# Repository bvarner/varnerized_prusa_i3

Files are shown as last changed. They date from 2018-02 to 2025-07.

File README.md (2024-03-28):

# Varnerized Prusa i3 3D Printer Clone

This is a project to produce a 3d printer based upon the (very excellent) work of Mr. Josef Prusa, and the 3d printing community at large.

After playing with an i3 MK2.5 my office at the time acquired I found some guides online for building your own printer inspired by the Prusa design.
Specifically, [Tom's Dolly Build](https://toms3d.org/2017/02/23/building-cheapest-possible-prusa-i3-mk2/) was highly inspiring.

I'm willing to sacrifice _some_ asthetics, a bit of performance, the 'ease' of pre-integration, and get an education for the sake of cost cutting.
As in the early heady days of the PC industry... building a 'clone' from imported components is cheaper than purchasing the fully assembled and configured machine.

## Goal of the project.

To clone a Prusa i3 with very similar mechanics, using import parts and cheaper, more-modular electronics.
My initial budget for the build is $225. With that budget, I produced a wooden framed i3 clone, using an Arduino & RAMPS board with A4988 stepper drivers, knockoff E3D V6 hotend, and an aluminum heated bed.

I have since upgraded some things considerably, in a price-conscious manner, and well behind the bleeding edge, so that I can source parts inexpensively.

This isn't just an attempt to build a clone and leave it alone. In keeping with the RepRap / Prusa mentality, my desire is to build a device that allows for replicating / designing / implementing more advanced subsequent generations.

## This Repository / Branch Strategy

The 'master' branch here will reflect the current (stable, functioning) state of the project - the machine I'm currently running, or the last state of the machine.
The 'development' branch will track be the next iteration of updates / upgrades.

# 1.3 - Volcano Hotend & Belt Tensioning
Over the years I've had problems with bearings coming loose from the x-axis ends. I held them in place with zip-ties for more than a year.
My pancake stepper with the skelestruder gave me phenomical prints, but I had many problems with stability of the hotend holding temp during high extrusion rates or aggressive part cooling fan use.

In order to print things faster (I'm sick of waiting four hours for a tiny part) and with thicker layers, I have upgraded to a Volcano knock-off hotend -- which the skelestruder supports beautifully.
I've also decided to print my entire hotend assembly in polycarbonate, as I was having multiple parts sag over time and when printing high-temp filaments (like PC or nylon).

I ended up having to upgrade to a slightly larger pancake motor, as I exceeded the torque of the tiny pancake before I exceeded the reasonable flow rate of a 0.6mm CHT volcano nozzle.

A 200g spool of PC is more than enough to print the entire extruder and omega several times over.

Credits to the folks who made these fantastic parts that I'm using:
[X-Axis](https://www.printables.com/model/394668-mk225s-x-axis-revision-with-belt-tensioner)
[Y-Axis Tensioner](https://www.printables.com/model/306303-y-axis-belt-tensioner-v2)

# 1.2 - Skelestruder.
Having some shore 95A flex filament to print, the MK3 extruder design is rubbish. I've had issues with part cooling, part visibility during print, z-axis adjustment, it's been a problem. Futhermore I get a lot of obvious print quality issues with linear advance and the direct drive extruder with 1/16th step division.
The [Skelestruder](https://www.thingiverse.com/thing:2845416) is designed to address all of that, and after having it for a few weeks, it was obvious it's a superior design.

Additionally, a friend of mine supplied me with a Prusa Mini+ filament sensor kit, which I've integrated into my build using 
this [skelestruder sensor cover](https://www.thingiverse.com/thing:4235461).

Initially I printed everything in PETG, without a silicone sock and insulation at the top of the heat block. This caused EcageS to melt a couple times, and deformed some other parts when I attempted to print Nylon at high-temperatures.
To combat this problem, I've reprinted some parts in Polycarbonate. I purchased a 200g trial spool for a reasonable fee.

* Printed Parts
    * Polycarbonate
        * SP_EcageS_r1.stl
        * SP_Omega_r2.stl
        * SP_Pinion16_r1.stl
        * SP_Pinion14_r1.stl
        * [SP_Xclamp_mk2.stl](https://www.thingiverse.com/thing:3699231)
    * PETG
        * SP_Carriage_r1.stl
        * SP_tail_b2.stl
        * SP_EcageB_r1.stl
        * SP_EcageF17_r1.stl
        * SP_Shroud_r1.stl
        * SP_Key_r1.stl
        * Inlet_ptfe_r1b.stl
        * SP_Spider17_r1.stl
        * SP_Wheel_r1.stl
        * SP_Tread56_r1.stl
        * SP_Prack_r1.stl
        * SP_Idler_r1.stl
        * SP_tensioner_b1.stl
        * SP_knob_b2.stl
        * SP_spacer_v1a4.stl
        * IR_Sensorcover_top.stl
        * IR_Sensorcover_outlet.stl
        * IR_Sensorcover_bottom.stl
        * IR_Sensor_Arm.stl
* Purchased Parts
    * [GT2 140-2GT-6](https://www.amazon.com/gp/product/B014QJBVOY/ref=ppx_yo_dt_b_asin_title_o00_s00?ie=UTF8&psc=1)
    * [Polyimide (Kapton) tape](https://www.amazon.com/gp/product/B00W3FAFP0/ref=ppx_yo_dt_b_asin_title_o04_s00?ie=UTF8&psc=1)
    * [105zz bearings](https://www.amazon.com/gp/product/B00ZHSTKCE/ref=ppx_yo_dt_b_asin_title_o07_s00?ie=UTF8&psc=1)
    * [5mmx100mm shafts](https://www.amazon.com/gp/product/B01B27MJC6/ref=ppx_yo_dt_b_asin_title_o07_s01?ie=UTF8&psc=1) I cut and shaped these with an angle grinder.
    * [12v 5015 fans](https://www.amazon.com/gp/product/B07LF1V1P1/ref=ppx_yo_dt_b_asin_title_o07_s01?ie=UTF8&psc=1) My original cooling fan died.
    * [Prusa IR filament sensor](https://www.aliexpress.com/item/32976810546.html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)
    * [Heatblock Top Insulation](https://www.amazon.com/gp/product/B075CST527/ref=ppx_yo_dt_b_asin_title_o08_s00?ie=UTF8&psc=1) I used this between the heatbreak and the heatblock.
    * [Heatblock Silicone Sock](https://www.amazon.com/gp/product/B07Q3KHL6R/ref=ppx_yo_dt_b_asin_title_o09_s00?ie=UTF8&psc=1) How did I go so many years without a silicone sock?

# 1.1.1 - Lack Table Enclosure.
Following the [prusaprinters blog post](https://blog.prusaprinters.org/cheap-simple-3d-printer-enclosure/) on building an inexpensive (hah!) enclosure for your printer I recently picked up a couple of Ikea LACK tables.
After getting local quotes for producing the 440x440 and 440x220 acrylic panels, I opted to buy a set from a vendor on Amazon who could beat the locally sourced prices.

* Printed Parts
    * PSU Shroud
        * Compatible with the Prusa Lack table mounting clip (mounting foot geometry is closer to the Prusa part)
        * Added Lack Table PSU retainer. Similar Style as the Prusa version.
        * Text rotates to the upside down orientation on the PSU Shroud if you're rendering the LACK table parts.
    * [Ikea LACK Enclosure Main Parts](https://www.thingiverse.com/thing:2864118)
    * [Frame brace replacing the PSU for the MK3](https://www.thingiverse.com/thing:2859884)
    * [60 degree heatbed cable cover for the MK3](https://www.thingiverse.com/thing:2890592)
    * [608 bearing wheels for the adjustable spool holder](https://www.thingiverse.com/thing:3791583)
    * [Prusa Enclosure Bottom Corner with more cable space](https://www.thingiverse.com/thing:3067172)
    * [IKEA Lack Table Stack Coupler](http://www.thingiverse.com/thing:3488697)
* Purchased Parts
    * #12 AWG Silicone wire. So much better to work with than THHN.
    * XT60H Connectors
    * misc. dupont connectors & hookup wire (from the scrap bin)
    * (3) IRLB3034 N-Channel Mosfets & 10k Ohm 0805 SMT Resistors.
    * 12v RGB LED 5050 Strip (I had leftovers from another home project)
* @Home Fabricated PCB For Controlling RGB LEDs
    * Check the LEDControl directory for full KiCAD project.
    * Perfect for home-based acid etching and SMT hand soldering.
    * I use the 'laser-printer hot-iron transfer' method, and it works quite well.

# 1.1.0 - More MK3 less, MK2.
Total upgrade cost was ~$75 in January 2018.

* Heat-Bed
    * I replaced my aluminum MK3 heat bed with a magnetic MK52, 12V heat bed.
    * It's not as 'flat' as the prusa originals.
    * Cost was ~$36, as opposed to the original one which was ~$8.
    * Spring steel sheet + PEI cost around another $25. At this time, I'd opt for the powder-coated textured spring steel instead.
* Extruder
    * Uses the BondTech style extruder pulleys
    * Improved part cooling
    * 5v Noctua Fan reduces ambient noise considerably
    * I did not add a filament sensor (yet) or a dust-buffer (yet).
* Electronics
    * After having beefed up the ampacity of the RAMPS 1.4a board, and replacing the heatbed mosfet, I decided to try a RAMPS 1.6 board.
    * Much better experience than the RAMPS 1.4a.
    * After 11 months of use, no over-heating issues. No fried mosfets, no fire risk. Much better electronics from that stand point.
    * Heat bed does heat slowly, a consequence of the mosfet choice on this board, from what I understand.
    * I've updated my firmware to Marlin 1.1.9, and "Varnerized" it to match the Prusa Home Screen Asthetic on the LCD.
    * Updated RAMBo cover a bit. I ended up reprinting in PETG and got much better results than with the original PLA. It also hasn't sagged and melted in my hot-box.
* Mechanics
    * Y-Axis bearing holders have been redone, and are now my own design that allows for slight play.
    * I think I've fixed the issues with the y-axis belt holder not contacting the limit switch properly.
    * Updates to the TR8_couplings have resulted in much better Z-axis stability.
    * heatbed cable cover -- based on using ring terminals and heavy gauge speaker wire -- is _very_ large compared to the MK3.

# 1.0.0 - Hybrid MK2s & MK3
The original starting point. 1 Spool of ABS, a few scraps of cabinet grade plywood, access to a working MK2, and about $165 in imported parts.

* Heat-Bed - I chose a 3mm thick aluminum MK3 (Ultimaker clone) 200x200mm.
    * This gives me a slightly smaller build area than an Original Prusa.
    * No 'fully-automatic' skew compensation.
        * The aluminum bed of the MK3 will still work for automatic z-layer leveling.
        * Guided x-y skew measurement and compensation will be required.
    * I did pony up for a sheet of PEI plastic to cover the aluminum bed and improve adhesion. That was worth it.
* Steppers - I used an inexpensive 5-pack of 5mm output shaft steppers that put out ~40n-cm of torque.
    * My Z-Axis motors require couplings to the lead screws.
    * I did pony up for T8 ACME lead screws and nuts for the Z-axis. The small cost should be worth the improved ridgidity and accuracy.
* Electronics - Arduino Mega 2650 + RAMPS 1.4a
    * Won't be nearly as nicely packaged as a mini-rambo... until I print my own case design to make it not ugly.
    * Will have to custom-compile firmware from the Marlin project.
    * More flexibility in the long-run with regards to expansion and addition of other sensors.
    * I used a 30Amp, 12v power supply (360 Watt). I was able to get this for $20 from Amazon, which was only slightly more expensive than the best priced 240Watt imported supply. Low quantities of heavy items are expensive to ship.
    * I'm going to just bypass the poly-fuses on the RAMPS board and add properly sized inline fuses. Perhaps someday I'll replace the RAMPs board. Perhaps Not.
* Frame - I'm making mine out of wood.
    * Won't be as svelt as a Prusa from the side, and may warp / twist slightly with seasonal changes. I'll be using thing-laminations of quarter-sawn lumber or cabinet-grade plywood to minimize this.
    * Major reduction of cost here. An MK2 aluminum frame runs ~$70. Laser-cut acrylic and wood are cheaper, but less rigid, and won't be as nice as mine.
    * Basing off the MK3 frame (which uses 3030 extrusions rather than threaded rods) translates more easily to wood.
    * I have a pretty well equipped wood shop, with 40 year old tools that are accurate +- 0.254mm and within a half-degree of cross-cut. I have calipers. I'll be able to correct for skew. :-)

## Printed Parts Lineage / Changes

* Y-Axis (under heatbed carriage) -- Mostly from the MK3. The necessity of an endstop swtich necessitates some changes to the Y-Motor mount. I am expecting to need to modify the rear frame DXF to reflect modifications / changes. I may not have room for the limit switch microswitch. Also, the belt holder for y-frame may need modification.
* X-Axis (gantry above heatbed) -- Completely from the MK2s.
* Z-Axis -- Mostly from the MK3. The T8 leadscrew will likely extend beyond the upper limit of the MK3 frames upper z-ends. I modified the MK3 parts to 'open' the top of the leadscrew holes and the rod holding hole -- ala a MK2/s. I figure this will be easier than cutting a T8 rod.
* Extruder -- Completely from the MK2s. I may look into the cogged dual-feed of the MK3 at some point, but until the Prusa fillament sensor board clones start to appear, there's really no reason to do that.
    * I will need to wait until my induction probe arrives to make sure it's the same physical size as the PINDA and avoid re-printing.
    * Thankfully for the Z-axis I don't need an end-stop limit switch.
* LCD -- Assuming my LCD fits the frame properly, I'll use the Prusa design...

### Print Settings

Prusa uses ABS, 20% infill, 3 perimeter (vertical) shells on a 0.4mm nozzle. The rest, well that's up to you. :-)
The three vertical shells are incredibly important. The extra ridigity / support is _really_ necessary, or you're likely to break idler parts.

### BOM

The basic BOM is:

| Part | Quantity |
| ---- | ---:|
| [extruder-body.stl](Printed-Parts/stl/extruder-body.stl) | 1 |
| [extruder-cover.stl](Printed-Parts/stl/extruder-cover.stl) | 1 |
| [extruder-idler.stl](Printed-Parts/stl/extruder-idler.stl) | 1 |
| [fan_nozzle.stl](Printed-Parts/stl/fan_nozzle.stl) | 1 |
| [LCD-cover-Varnerized-MK3.stl](Printed-Parts/stl/LCD-cover-Varnerized-MK3.stl) | 1 |
| [lcd-supports.stl](Printed-Parts/stl/lcd-supports.stl) | 1 |
| [lcd-knob.stl](Printed-Parts/stl/lcd-knob.stl) | 1 |
| [x-carriage.stl](Printed-Parts/stl/x-carriage.stl) | 1 |
| [x-end-idler.stl](Printed-Parts/stl/x-end-idler.stl) | 1 |
| [x-end-motor.stl](Printed-Parts/stl/x-end-motor.stl) | 1 |
| [y-belt-holder.stl](Printed-Parts/stl/y-belt-holder.stl) | 1 |
| [y-belt-idler.stl](Printed-Parts/stl/y-belt-idler.stl) | 1 |
| [y-holder.stl](Printed-Parts/stl/y-holder.stl) | 4 |
| [y-motor-holder.stl](Printed-Parts/stl/y-motor-holder.stl) | 1 |
| [z-axis-bottom.stl](Printed-Parts/stl/z-axis-bottom.stl) | 1 |
| [z-axis-top.stl](Printed-Parts/stl/z-axis-top.stl) | 1 |

Optionally, I highly recommend you print the spool holder, RAMPS (Rambo) case, psu shroud, etc. or: model your own.

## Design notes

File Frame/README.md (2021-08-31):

# Varnerized Prusa i3 Clone
## MK3 - Frame & X-Y Carriage

This frame can accomodate original prusa 250x210 heatbeds (the MK42 or MK43, as well as MK52). 
You'll need a build surface of 250x210 to print some of these.

In this folder you'll find:

* The original Prusa MK3v8b.dxf.
* DXfs which extract the frame (and m3 mount holes) into separate DXfs.
* OpenSCAD files which slice the DXFs into layers, suitable for printing -- for use as router templates. :-)
* STLs of each segment of the OpenSCAD templates.

I produced these by:

1. Downloading the prusa original dxf.
2. Opening the DXF in DraftSight.
    * Separating the carriage into a different DXF.
    * Tracing the Spline in the original Prusa frame with a polyline.
5. Setting up OpenSCAD files that create lap-joints of the OpenSCAD sources, and then rendered each section of the dxfs to STL.

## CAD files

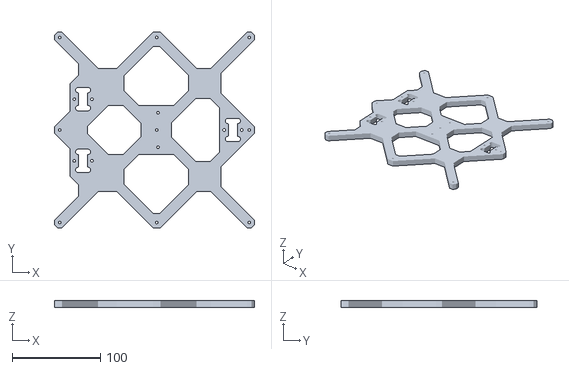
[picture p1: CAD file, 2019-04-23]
Frame/MK3-carriage-full.stl
227.0 x 222.0 x 8.00

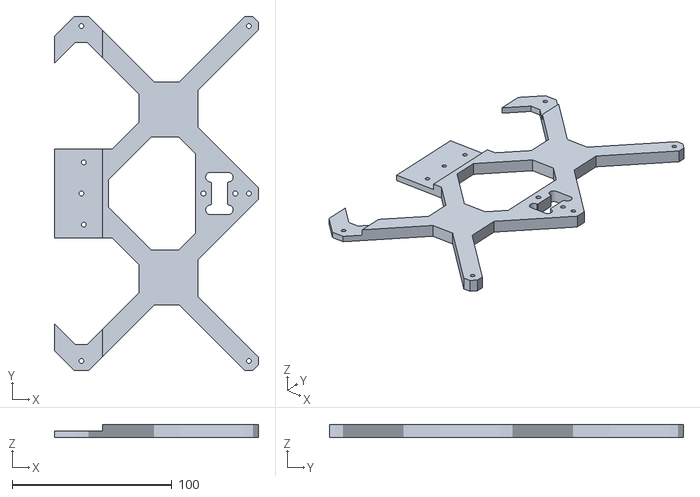
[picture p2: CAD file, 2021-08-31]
Frame/MK3-carriage-2.stl
127.9 x 222.0 x 8.00

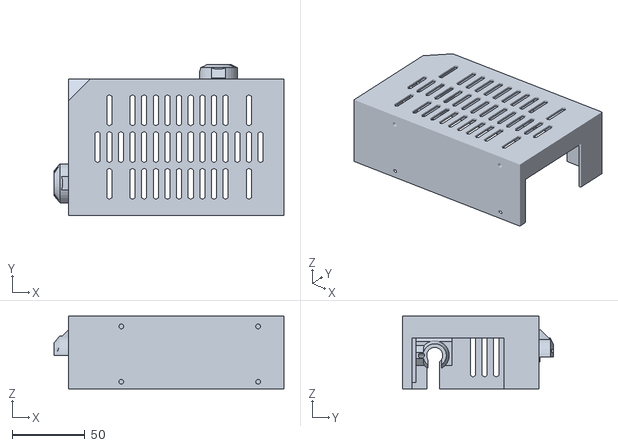
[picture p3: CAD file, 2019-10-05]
Printed-Parts/scad/ramps_case/case2_top.stl
158.1 x 103.5 x 50.0

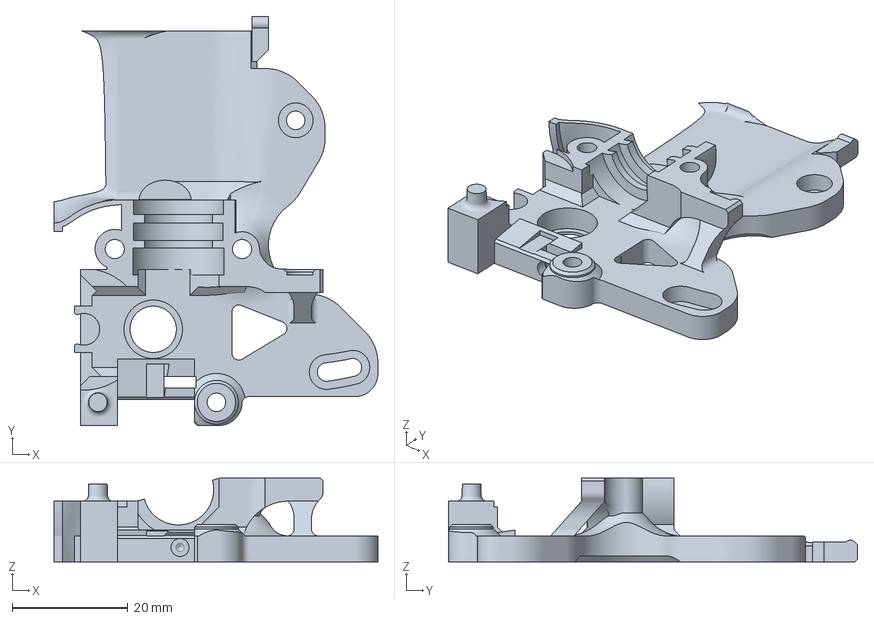
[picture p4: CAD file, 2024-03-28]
Printed-Parts/skelestruder/PC/SP_EcageF17_r1.3mf
56.0 x 70.7 x 14.5 mm

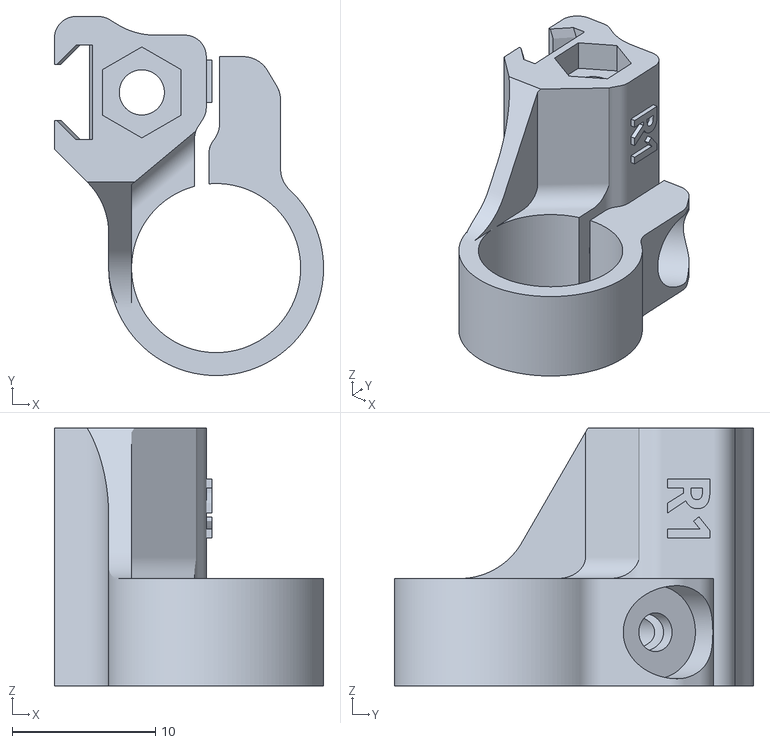
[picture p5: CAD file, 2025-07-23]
Printed-Parts/skelestruder/PETG/SP_Prack-M12.stl
18.8 x 25.1 x 18.0

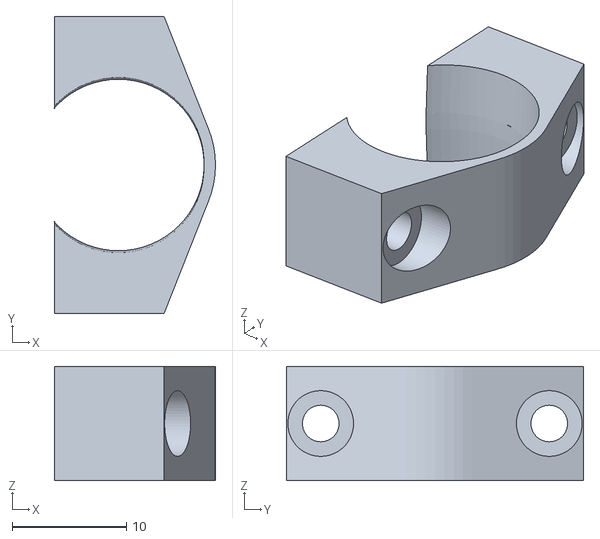
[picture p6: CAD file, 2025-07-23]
Printed-Parts/stl/y-carriage-bearing-holder.stl
14.1 x 26.0 x 10.0

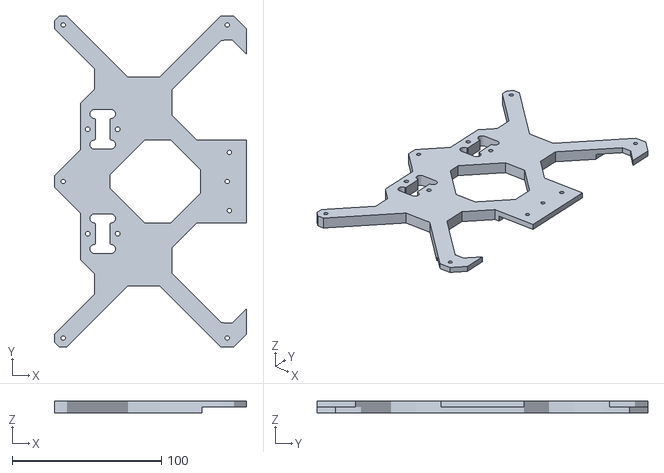
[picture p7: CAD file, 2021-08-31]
Frame/MK3-carriage-1.stl
129.1 x 222.0 x 8.00

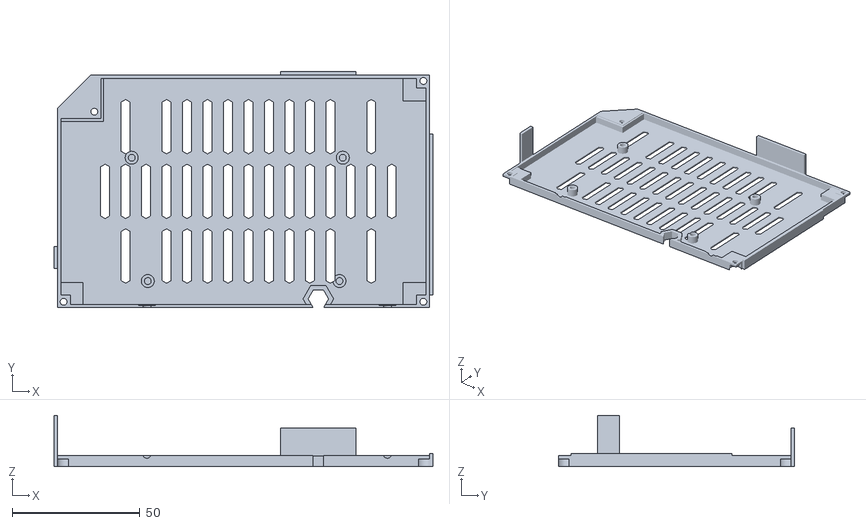
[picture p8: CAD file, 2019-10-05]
Printed-Parts/scad/ramps_case/case2_bottom.stl
148.1 x 92.4 x 20.0

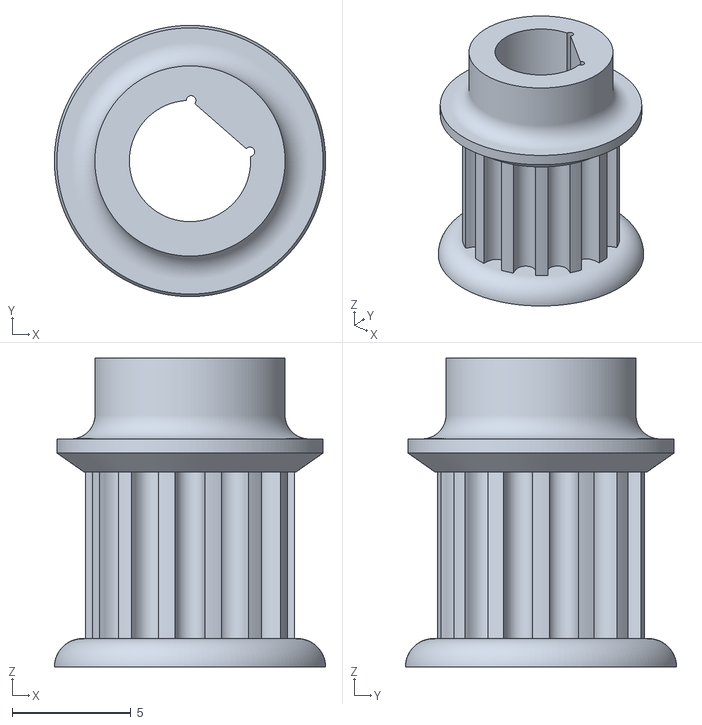
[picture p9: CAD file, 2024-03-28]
Printed-Parts/skelestruder/PC/SP_Pinion14_r1.stl
11.4 x 11.4 x 13.0

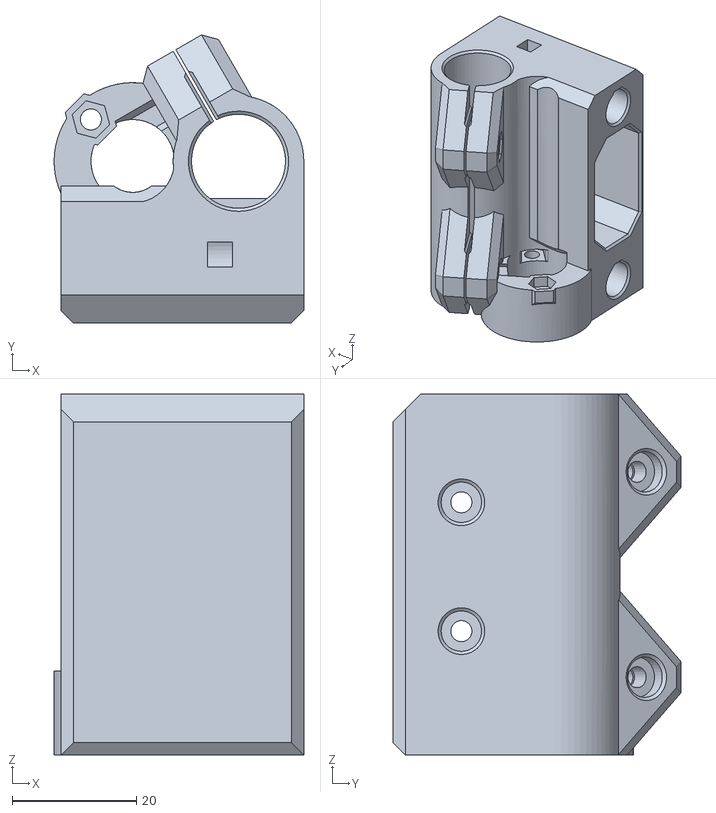
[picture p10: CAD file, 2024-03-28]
Printed-Parts/stl/x-end_idler_boogie.stl
40.1 x 46.3 x 58.0

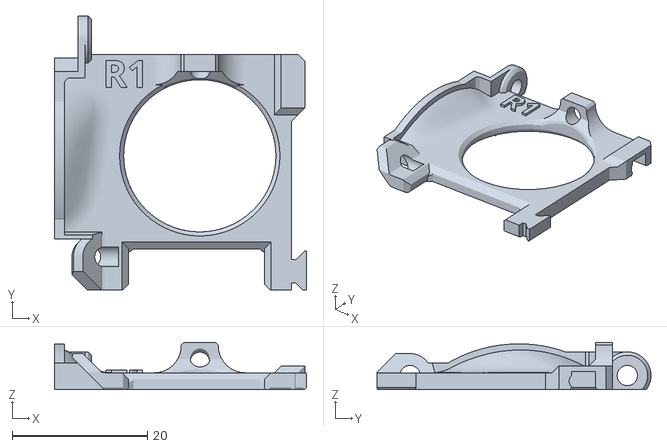
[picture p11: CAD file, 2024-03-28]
Printed-Parts/skelestruder/PC/SP_EcageS_r1.stl
37.3 x 40.5 x 7.00

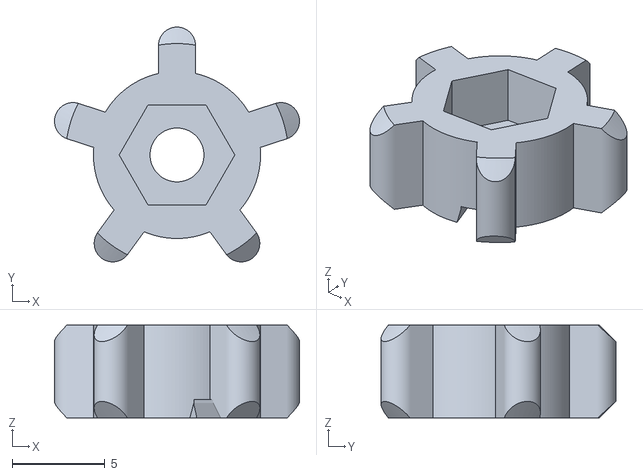
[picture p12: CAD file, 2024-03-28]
Printed-Parts/skelestruder/PETG/SP_knob_b2.stl
13.2 x 12.7 x 5.00

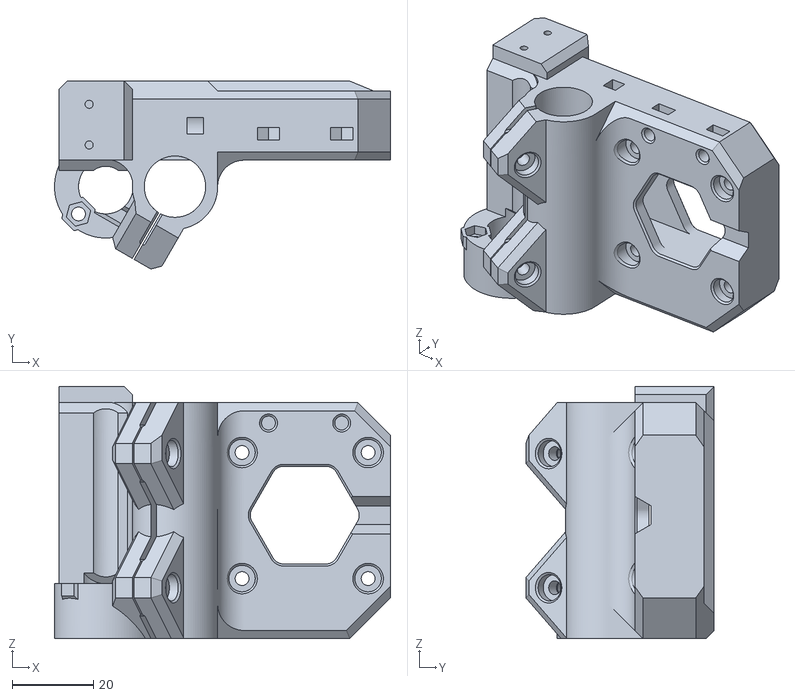
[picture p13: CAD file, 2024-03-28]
Printed-Parts/stl/x-end_motor_with_sensor.STL
82.6 x 46.3 x 62.0

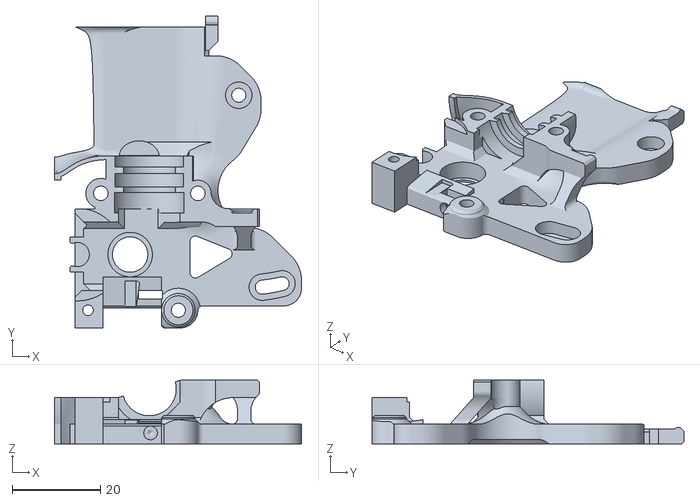
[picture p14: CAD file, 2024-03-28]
Printed-Parts/skelestruder/PC/SP_cageF17_Varnerized.stl
56.0 x 70.7 x 14.5

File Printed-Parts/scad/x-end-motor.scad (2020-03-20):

// PRUSA iteration3
// X end motor
// GNU GPL v3
// Josef Průša <iam@josefprusa.cz> and contributors
// http://www.reprap.org/wiki/Prusa_Mendel
// http://prusamendel.org

use <x-end.scad>

module x_end_motor_base(){
 x_end_base();
 translate(v=[-15,31,26.5]) cube(size = [17,44,53], center = true);
}

module x_end_motor_endstop_base(){
    translate([-23.5,-28.5,58]){
        difference(){
            // Base block
            cube([17,18.2,4]);
            // Nice edge
            translate([-1,10,10])rotate([-45,0,0])cube([20,20,20]);
            } 
        }
}

module x_end_motor_endstop_holes(){
    translate([-23.5,-28.5,58]){
        translate([17/2,5,-3]){
            // Back screw hole for endstop
            translate([-3.25,0,0]) cylinder(r=1,h=19,$fn=20);
            translate([-3.25,0,6]) cylinder(r1=1, r2=1.5, h=2,$fn=20);
            // Front screw hole for endstop
            translate([3.25,0,0]) cylinder(r=1,h=19,$fn=20);
            translate([3.25,0,6]) cylinder(r1=1, r2=1.5, h=2,$fn=20);
            }
        }
}



module x_end_motor_holes(){
 x_end_holes();
 // Position to place
 translate(v=[-1,32,30.25]){
  // Belt hole
  translate(v=[-14,1,0]) cube(size = [10,46,22], center = true);
  // Motor mounting holes
  translate(v=[20,-15.5,-15.5]) rotate(a=[0,-90,0]) rotate(a=[0,0,90]) cylinder(h = 70, r=1.8, $fn=30);
  translate(v=[1,-15.5,-15.5]) rotate(a=[0,-90,0]) rotate(a=[0,0,90]) cylinder(h = 10, r=3.1, $fn=30);
  translate(v=[20,-15.5,15.5]) rotate(a=[0,-90,0]) rotate(a=[0,0,90]) cylinder(h = 70, r=1.8, $fn=30);
  translate(v=[1,-15.5,15.5]) rotate(a=[0,-90,0]) rotate(a=[0,0,90]) cylinder(h = 10, r=3.1, $fn=30);
  translate(v=[20,15.5,-15.5]) rotate(a=[0,-90,0]) rotate(a=[0,0,90]) cylinder(h = 70, r=1.8, $fn=30);
  translate(v=[1,15.5,-15.5]) rotate(a=[0,-90,0]) rotate(a=[0,0,90]) cylinder(h = 10, r=3.1, $fn=30);
  translate(v=[20,15.5,15.5]) rotate(a=[0,-90,0]) rotate(a=[0,0,90]) cylinder(h = 70, r=1.8, $fn=30);
  translate(v=[1,15.5,15.5]) rotate(a=[0,-90,0]) rotate(a=[0,0,90]) cylinder(h = 10, r=3.1, $fn=30);

  // Material saving cutout 
  translate(v=[-10,12,10]) cube(size = [60,42,42], center = true);

  // Material saving cutout
  translate(v=[-10,40,-30]) rotate(a=[45,0,0])  cube(size = [60,42,42], center = true);
  
 }
}

// Motor shaft cutout
module x_end_motor_shaft_cutout(){
    union(){
    difference(){
        translate(v=[0,32,30]) rotate(a=[0,-90,0]) rotate(a=[0,0,90]) cylinder(h = 70, r=17, $fn=6);
       
        translate(v=[-10,-17+32,30]) cube(size = [60,2,10], center = true);
        translate(v=[-10,-8+32,-15.5+30]) rotate(a=[60,0,0]) cube(size = [60,2,10], center = true); 
        translate(v=[-10,8+32,-15.5+30]) rotate(a=[-60,0,0]) cube(size = [60,2,10], center = true);
        
        
    }
    translate(v=[-30,25.2,-11.8 +30]) rotate(a=[0,90,0]) cylinder(h = 30, r=3, $fn=30);
    translate(v=[-30,19.05,30]) rotate(a=[0,90,0]) cylinder(h = 30, r=3.5, $fn=100);
}
}



module selective_infill()mirror([0,1,0]) translate([-50, -33, 0.6])
{ 
   difference()
    {
    union()
    {
        difference()
        {
        translate([50,50,0.6]) rotate([0,0,90]) cylinder( h=6, r=11.7, $fn=30);//0, 17, 0.6
        translate([50,50,-1]) rotate([0,0,90]) cylinder( h=10, r=11.5, $fn=30);
        }
        difference()
        {
        translate([50,50,0.6]) rotate([0,0,90]) cylinder( h=6, r=10.7, $fn=30); //0, 17, 0.6
        translate([50,50,-1]) rotate([0,0,90]) cylinder( h=10, r=10.5, $fn=30);
        } 
        difference()
        {
        translate([50,50,0.6]) rotate([0,0,90]) cylinder( h=6, r=9.9, $fn=30); //0, 17, 0.6
        translate([50,50,-1]) rotate([0,0,90]) cylinder( h=10, r=9.7, $fn=30);
        } 
        difference()
        {
        translate([50,50,0.6]) rotate([0,0,90]) cylinder( h=6, r=9, $fn=30); //0, 17, 0.6
        translate([50,50,-1]) rotate([0,0,90]) cylinder( h=10, r=8.8, $fn=30);
        } 
    }
    translate([57.5,50.5,-1]) rotate([0,0,45]) cube([8,10,9]); // front
    translate([52,30.5,-1]) rotate([0,0,45]) cube([10,20,20]);  // front angled
    translate([32,35.5,-1]) cube([8,30,9]); // inner horizontal
    }
   } 
   
 module reinforcement_selective_infill()
   {
    rotate([90,0,-15,]) translate ([-1.5, 8, 26])linear_extrude(height = 0.2) polygon( points=[[-2,0],[0,12],[8,0]] ); //bearings
    
    rotate([90,0,-50,]) translate ([8.5, 8, 1.4])linear_extrude(height = 0.2) polygon( points=[[0,0],[0,12],[8,0]] ); //body
    
    }
    
   
// Final part
module x_end_motor(){
 difference(){
     union(){
            x_end_motor_base();
            x_end_motor_endstop_base();
            
         }
  x_end_motor_shaft_cutout();
  x_end_motor_holes();
  x_end_motor_endstop_holes();      
  selective_infill();
  reinforcement_selective_infill();
         
      translate([-12,-42,65]) rotate([-35,0,0])  rotate([0,0,45]) cube([10,10,10]);
      translate([-15,8.5,6]) rotate([90,0,0]) cylinder(h=5, r=5, $fn=30);   
      translate([-15,8.5,51]) rotate([90,0,0]) cylinder(h=5, r=5, $fn=30);   
      translate([-15,3.5,6]) rotate([90,0,0]) cylinder(h=3, r1=5, r2=4, $fn=30);   
      translate([-15,3.5,51]) rotate([90,0,0]) cylinder(h=3, r1=5, r2=4, $fn=30); 
 }
}

x_end_motor();

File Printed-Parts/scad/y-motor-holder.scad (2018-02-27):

// PRUSA iteration4
// Y motor holder
// GNU GPL v3
// Josef Průša <iam@josefprusa.cz> and contributors
// http://www.reprap.org/wiki/Prusa_Mendel
// http://prusamendel.org

module endstop_mount() {
    difference() {
        union() {
            translate([-21+6,8,0]) cube([12-2, 5, 28]);    
            translate([-21,8-5,0]) cube([9, 10, 28]);
        }
        translate([-16,16,11]) rotate([90,0,0]) cylinder(h = 10, r=0.8, $fn=20);
        translate([-16,13.2,11]) rotate([90,0,0]) cylinder(h = 2, r1=1.2, r2=0.8, $fn=20);

        translate([-16,16,17.5]) rotate([90,0,0]) cylinder(h = 10, r=0.8, $fn=20);
        translate([-16,13.2,17.5]) rotate([90,0,0]) cylinder(h = 2, r1=1.2, r2=0.8, $fn=20);
        
        translate([-22,13.2,24.5]) rotate([90,0,0]) rotate([0, 0, 45]) cube([5, 4, 4]);
    }
}

module holder()
{
    difference()
    {
        // base body
        translate([-6,-1.5,0]) cube([19,42,47]);

        // shape cuts
        translate([-20,19.5,26]) rotate([0,90,0]) cylinder( h=35, r=12, $fn=30 );   
        translate([-11,20,15]) cube([26,23,64]);
        translate([-20,5.5,-1]) cube([26,41,64]);
        translate([-20,-5,37]) cube([26,21,20]);
        translate([-20,-1,37]) cube([26,30,20]);
        
        // lower motor screw
        translate([-20,35 ,10.5]) rotate([0,90,0]) cylinder( h=40, r=1.65, $fn=30 ); 
        translate([-7,35,10.5]) rotate([0,90,0]) cylinder( h=15, r=3.1, $fn=30 );         
        
        // upper motor screw    
        translate([-20,4,41.5]) rotate([0,90,0]) cylinder( h=40, r=1.65, $fn=30 );         
        translate([4,4,41.5]) rotate([0,90,0]) cylinder( h=4, r=3.1, $fn=30 );         
        
        // lower frame screw    
        translate([0,12,7]) rotate([90,0,0]) cylinder( h=40, r=1.6, $fn=30 ); 
        translate([0,7,7]) rotate([90,0,0]) cylinder( h=5, r=3.2, $fn=6 ); 
        translate([0,6.6,7]) rotate([90,0,0]) cylinder( h=2, r2=3.2, r1=4, $fn=6 ); 
        
        // upper frame screw    
        translate([0,12,29]) rotate([90,0,0]) cylinder( h=40, r=1.6, $fn=30 ); 
        translate([0,7,29]) rotate([90,0,0]) cylinder( h=5, r=3.2, $fn=6 ); 
        translate([0,6.6,29]) rotate([90,0,0]) cylinder( h=2, r2=3.2, r1=4, $fn=6 );

        // corners
        translate([-10,20,42]) rotate([45,0,0]) cube([60,10,10]);        
        translate([-10,-5,42]) rotate([45,0,0]) cube([60,10,10]);        
        translate([-10,38,-7]) rotate([45,0,0]) cube([60,20,10]);        
        translate([-10,43,10]) rotate([45,0,0]) cube([60,20,20]);  
        translate([-14,-10,-2]) rotate([0,45,0]) cube([10,50,10]);        
// Removed for end-stop
//        translate([-14,-10,37]) rotate([0,45,0]) cube([10,50,10]);
        translate([18,-10,-5]) rotate([0,0,45]) cube([10,10,60]);        
    }
    
    // end-stop reinforcement
    translate([-15, -1.5, 29]) cube([9, 8, 5]);
    translate([-15, -1.5, 29]) rotate([0, 45, 0]) cube([14, 7, 6.5]);
    
    // reinforcement
    translate([7.8,1.9,0]) rotate([0,0,55]) cube([5,5,18]);
    difference()
        {
            translate([7.8,1.9,13.6]) rotate([0,0,55]) cube([5,5,23.4]);
            translate([-20,19.5,26]) rotate([0,90,0]) cylinder( h=35, r=12, $fn=30 );   
        }
   
}

module y_motor_holder()
{
//    rotate([0,90,0])
    difference()
        {
            union() {
                holder();
                translate([13, -6.5, 26])  rotate([-90, 0, 0]) rotate([0, 90, 180]) endstop_mount();
            }
            
        // enstop_mount_cleanup....
        translate([18,-10,-5]) rotate([0,0,45]) cube([10,10,60]); 
        translate([-20,19.5,26]) rotate([0,90,0]) cylinder( h=35, r=12, $fn=30 );   
        translate([0,10,29]) rotate([90,0,0]) cylinder( h=4.5, r=4,  $fn=6 );

        // Upper motor mount screw
        translate([-21, 0, 0]) translate([4,4,41.5]) rotate([0,90,0]) cylinder( h=25, r=3.1, $fn=30 );         
            
        // selective infill
        translate([-0,1,33]) cube([12,0.5,2]);        
        translate([-3,1,2]) cube([15,0.5,1]);        
        translate([-5,1.5,13]) cube([17,0.5,8]);        
        
        //version
        translate([-1,-1,15]) rotate([90,0,0]) linear_extrude(height = 0.6) 
        { text("R1",font = "helvetica:style=Bold", size=5, center=true); }
        }
}    
    
y_motor_holder();    
    
    
    

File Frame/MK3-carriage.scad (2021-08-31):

// Prusa i3 MK3V8B Carriage routing template.

/* --- Print Settings ---
    Rotate stl outputs in your slicing software to avoid support material.
    All layers: 0.25mm
    Infill: 10% honeycomb
    you may want to compensate for elephant foot.
*/
    
/* --- Use Notes ---
    Once all the parts are printed super-glue and clamp until cured.
    
    Use double-sided (carpet) tape to adhear the assembled frame to the wood when routing.
*/

// Select which sector to print ([1-2], or 0 for the full-size frame)
sector = 2;

// Final thickness of the frame.
// 6mm works, but recommend 8.
thickness = 8;

/* -- About the .dxf --
    I started with the .dxf obtained from the original Prusa github repo.
    I extracted the carriage bits from there using DraftSight.
*/
module layer() {
    
translate([-13, -10, 0])
linear_extrude(thickness, convexity = 10)
    import("MK3v8b-carriage.dxf", convexity = 10, $fn = 100);

}

if (sector == 1 || sector == 0) {
    union() {
        intersection() {
            layer();
            cube([100, 230, thickness / 2]);
        }
        intersection() {
            layer();
            translate([0, 0, thickness / 2])
                cube([130, 230, thickness / 2]);
        }
    }
}

if (sector == 2 || sector == 0) {
    union() {
        intersection() {
            layer();
            translate([100, 0, 0])
                cube([130, 230, thickness / 2]);
        }
        intersection() {
            layer();
            translate([130, 0, thickness / 2])
                cube([100, 230, thickness / 2]);
        }
    }
}

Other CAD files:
Printed-Parts/skelestruder/PETG/SP_EcageF17_r1.stl
Frame/MK3v8b.dxf
Printed-Parts/skelestruder/PETG/SP_Tread56_r1.stl
Printed-Parts/stl/Y-axis_belt_tensioner_2.stl
Frame/MK3-frame.scad
Frame/MK3-frame-1.stl
Frame/MK3-frame-2.stl
Frame/MK3-frame-3.stl
Frame/MK3-frame-4.stl
Frame/MK3-frame-6.stl
Frame/MK3-frame-7.stl
Frame/MK3-frame-8.stl
Frame/MK3-frame-9.stl
Frame/MK3-front-plate.dxf
Frame/MK3-front-plate.scad
Frame/MK3-front-plate.stl
Frame/MK3-rear-plate.dxf
Frame/MK3-rear-plate.scad
Frame/MK3-rear-plate.stl
Frame/MK3v8b-carriage.dxf
Frame/MK3v8b-frame.dxf
Printed-Parts/scad/LCD-cover-Varnerized-MK3.scad
Printed-Parts/scad/RAMBo-cover-base.scad
Printed-Parts/scad/RAMBo-cover-door-80mm_fan.scad
Printed-Parts/scad/RAMBo-cover-hinges.scad
Printed-Parts/scad/bearing.scad
Printed-Parts/scad/heatbed-cable-cover.scad
Printed-Parts/scad/lcd-supports.scad
Printed-Parts/scad/lcd_knob.scad
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

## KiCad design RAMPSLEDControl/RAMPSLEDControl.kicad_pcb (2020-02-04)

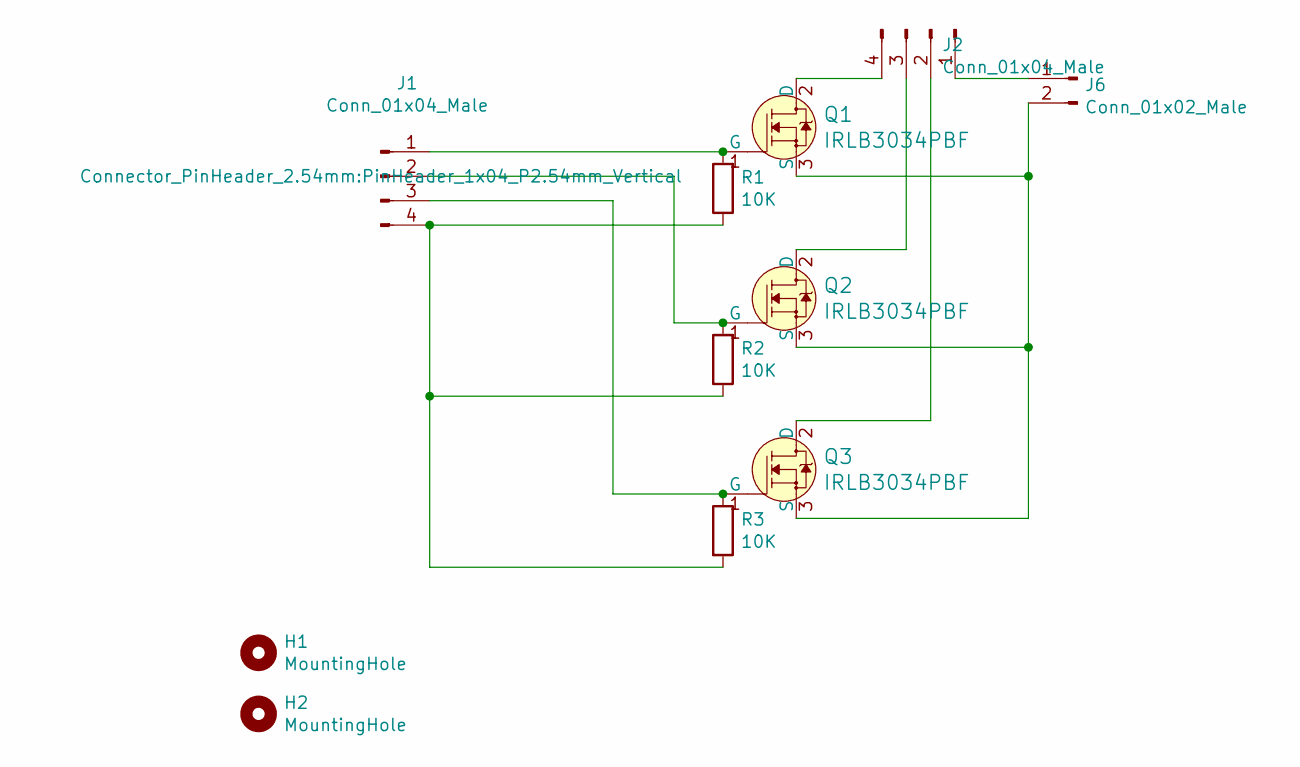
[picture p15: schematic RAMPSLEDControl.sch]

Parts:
H1, H2: MountingHole; MountingHole_3.2mm_M3_DIN965
J1: Conn_01x04_Male; PinHeader_1x04_P2.54mm_Vertical
J2: Conn_01x04_Male; PinHeader_1x04_P2.54mm_Horizontal
J6: Conn_01x02_Male; PinHeader_1x02_P2.54mm_Vertical
Q1, Q2, Q3: IRLB3034PBF; TO-220-3; MPN IRLB3034PBF; Digi-Key_PN IRLB3034PBF-ND
R1, R2, R3: 10K; R_0805_2012Metric_Pad1.15x1.40mm_HandSolder

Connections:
unnamed: J1.1, Q1.1 (G), R1.2
unnamed: J1.2, Q2.1 (G), R2.2
unnamed: J1.3, Q3.1 (G), R3.1
unnamed: J1.4, R1.1, R2.1, R3.2
unnamed: J2.1, J6.1
unnamed: J2.2, Q3.2 (D)
unnamed: J2.3, Q2.2 (D)
unnamed: J2.4, Q1.2 (D)
unnamed: J6.2, Q1.3 (S), Q2.3 (S), Q3.3 (S)

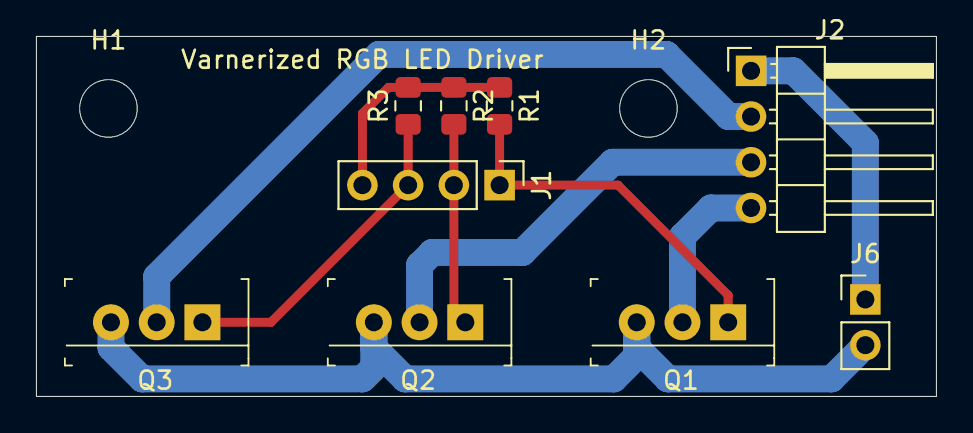
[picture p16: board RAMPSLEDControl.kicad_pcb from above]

Board: 2 copper layers, 50.0 x 20.0 mm, 11 parts (0 on the bottom side), 9 nets.

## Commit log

2018-01-05 Here we go. initial commit of my effort to turn the MK3 dxfs into STLs that can be used as a template.
    [MK3-carriage-1.stl, MK3-carriage-2.stl, MK3-carriage-4.stl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]
2018-01-09 Updates to the frame
    [MK3-carriage-1.stl, MK3-carriage-2.stl, MK3-carriage-4.stl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]
2018-01-10 Major adjustment. This should actually work now.
    [MK3-carriage-1.stl, MK3-carriage-2.stl, MK3-carriage-4.stl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]
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2018-01-10 Named folder to match original Prusa
    [MK3-carriage-1.stl, MK3-carriage-2.stl, MK3-carriage.scad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]
2018-01-11 Added the files and updates
    [LCD-cover-Varnerized-MK3.scad, LCD-cover-Varnerized-MK3.stl, bearing.scad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]
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2018-01-17 Bumped all this to 6mm thick, which is ~2x as thick
    [MK3-carriage-1.stl, MK3-carriage-2.stl, MK3-carriage.scad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]
2018-01-18 Updated the Extruder Body to move the P.I.N.D.A and Fan cable tray 'up' the extruder body, making more room for the non-Prusa 5mm probes, which seem to be longer.
    [extruder-body.scad, extruder-body.stl, extruder-main.scad]
2018-01-18 Better font on the Varnerized bits.
    [LCD-cover-Varnerized-MK3.scad, LCD-cover-Varnerized-MK3.stl]
2018-01-20 * Customized for smaller microswitch on the x-end. * Customized for T8 lead screws and accompanying brass z-nut rather than the Original Prusa bits.
    [x-end-idler.stl, x-end-motor.scad, x-end-motor.stl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]
2018-01-20 Modifying endstop location and hole spacing to match my microswitches.
    [y-motor-holder.scad, y-motor-holder.stl]
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2018-01-24 Added a PSU shroud. Wow. I really hate this scad source. It's nasty.
    [psu_shroud.scad, psu_shroud.stl]
2018-01-26 A 'clean room' remix of the PSU cover, based upon measurements from my PSU.
    [psu_shroud.scad, psu_shroud.stl]
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2018-01-26 Adjustments to hole locations, based on a print result.
    [psu_shroud.scad, psu_shroud.stl]
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2018-01-28 Updates to the y-belt-holder for limit switch clearance.
    [y-belt-holder.scad, y-belt-holder.stl]
2018-01-30 Undoing the unnecessary (and it would be kinda catastrophic) offset for the induction probe. Adding the cable holder.
    [cable-holder.scad, cable-holder.stl, extruder-body.stl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]
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2018-01-30 Added the POT cutout for the LCD supports. I chopped my finger with a steak knife manually making this modification....
    [lcd-supports.scad, lcd-supports.stl]
2018-02-17 Many adjustments based on working with the printer for a few days.
    * RAMBo based RAMPS cover. Lifted the original work from thingiverse. Proper credit in the files.
    * Reverse-engineered the lcd_knob with my micrometer and produced some openscad source. I have a reprint in progress (at 0.05 layers) I may have to tune this again.
    * The TR8 couplings have been updated with a longer D-shaft end, and a 'skirt' added to keep things from falling into the bearings.
    * Updates to the psu shroud, which I highly recommend you _don't_ print in ABS... unless you like layers stressing and breaking. I'll try it in PLA next time, but may end up springing for some nylon 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
    [RAMBo-cover-base.scad, RAMBo-cover-base.stl, RAMBo-cover-door-80mmfan.scad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]
2018-02-18 * LCD Knob. Because the Prusa repo used an STL to import into the SCAD (what the heck?) So I "clean-roomed" it from a physical print and my caliper. * A bit more pronounced recess in the PSU Shroud.
    [lcd_knob.scad, lcd_knob.stl, psu_shroud.scad]
2018-02-19 Minor tweaks to existing parts, and a spool holder.
    * PSU Shroud: Embossed the text a bit more.
    * TR8_coupling: Added a skirt to keep bits of plastic out of the bearing area. (probably totally unnecessary)
    * Added a Spool holder, inspired heavily by Martin Majewski's https://www.thingiverse.com/thing:1832235, but built with OpenSCAD.
    * I was just going to use Martin's, but I couldn't customize it properly to expand the hook area to accomodate the thickness of my frame. Bummer.
    * Only three printable parts. Arm, threaded bearing holder, nut..
    * Uses 608 bearings, without a need for a 'tire'.
    * Plenty of clearance for the extruder at max Z position. Based on the spacing, should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
    [psu_shroud.stl, spool_holder.scad, spool_holder_bearing_rod.scad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]
2018-02-27 Resync of the Rambo cover from thingiverse with the one from Prusa.
    Did some modifications to make an 80mm fan fit, but unfortunately, it's rubbing some things in there, so I haven't been able to mount it. :-/
    [RAMBo-cover-door-80mm_fan.scad, RAMBo-cover-door-80mm_fan.stl]
2018-02-27 Apparently I forgot to -a on the last commit.
    [RAMBo-cover-base.scad, RAMBo-cover-base.stl, RAMBo-cover-door-80mmfan.scad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]
2018-02-27 Updated the X-Ends to have a proper nut-trap for the brass TR-8 nuts.
    [x-end-idler.stl, x-end-motor.stl, x-end.scad]
2019-04-23 feat: A 5v PWM Fan Driver for the RAMPS board. fix: New bearing holder for the Y-Axis. feat: New, better z-axis couplers. feat: Fixed the y carriage belt holder. Forgot I had to actually cut part of 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
    [5vFanDriver.kicad_pcb, 5vFanDriver.sch, bearing.scad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]
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2019-10-05 Updated quite a few things. I've lost count. I think this is the RAMBo cover.
    [5vFanDriver.kicad_pcb, 5vFanDriver.sch, RAMBo-cover-base.scad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]
2019-10-05 I should clean these up later. Some of these cases are probably not the right one.
    [Extruder-cable-clip.scad, Extruder-cable-clip.stl, Heatbed-cable-clip_8mm.scad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]
2020-01-06 * Added a retainer (loosely based upon the Prusa one) for the PSU when mounting upside down on an Ikea LACK table. * Added a parameter for lack_table mounts which adds the upper retainer and flips th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
    [psu_shroud.scad]
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2020-02-04 Adding a KiCad Project that functions as an LED light control for 12v RGB lights.
    [RAMPSLEDControl.kicad_pcb, RAMPSLEDControl.sch]
2020-02-04 Parameterized the cable clearance.
    [psu_shroud.scad]
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2020-02-05 Nozzle fan holder STLs and the MK3 extruder body.
    [extruder-body.stl, extruder-cover.stl]
2020-02-05 * MK3 nozzle-fan. Somehow I missed having this exported to STL. * LEDControl project and PCB bits. * Updated Readme.
    [RAMPSLEDControl.kicad_pcb, RAMPSLEDControl.sch, nozzle-fan-holder.stl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]
2020-03-20 * Some minor cleanup and adjustments to the z-axis couplings. * Additional SCAD syntax cleanup. * Added the PrusaSlicer config.
    [x-end-motor.scad, z-axis-coupling.scad, z-axis-coupling.stl]
2021-08-31 Updating a few parts from a recent revision.
    [MK3-carriage-1.stl, MK3-carriage.scad, x-end.scad]
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2021-08-31 Skelestruder V1! * Cleanup older prusa parts that we don't use. * Add new skelestruder parts.
    [Extruder-cable-clip.scad, Heatbed-cable-clip_8mm.scad, Heatbed-cable-clip_8mm.stl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]
2021-09-06 Adding documentation for using the Skelestruder. I really like it's functionality. I'm hoping the Polycarbonate parts will avoid the 'melting' issues I've had with high-temperature filaments.
    [IR_Sensor_Arm.stl, IR_Sensorcover_bottom.stl, IR_Sensorcover_outlet.stl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]
2024-03-28 feat: Update X-Axis ends. feat: Update Y-Axis tensioner. feat: Updated to Skelestruder Volcano, and printed more parts in PC.
    [SP_EcageB_r1.3mf, SP_EcageF17_r1.3mf, SP_Spider17_r1.3mf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]
2025-07-23 chore: Pushing updates from my local machine. I'm not sure what changed here, it's been a _long_ time.
    [SP_Prack-M12.stl, y-carriage-bearing-holder.scad, y-carriage-bearing-holder.stl]
